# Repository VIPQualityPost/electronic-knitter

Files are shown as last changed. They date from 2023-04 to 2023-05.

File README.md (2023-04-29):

# Electronic Knitting Machine Controller
Inspired by the [Knitic project](https://github.com/mcanet/knitic), which 
seems to have mostly been abandoned. 
This board is to be a replacement for the mainboard within the machine, 
initially targeting Brother KH-930, KH-940 machines. While it disables the 
main touch controls, there is available a serial port which can control 
the patterns. Eventually, it would be nice to also design some 
compatibility with the original user interface panel. Additionally, the 
solenoid controls signals are exposed via HP 1650-63203 20-pin logic 
analyzer connector, either for debugging, or direct control of the 
solenoid array if you wish to just ignore the microcontroller on the 
board.

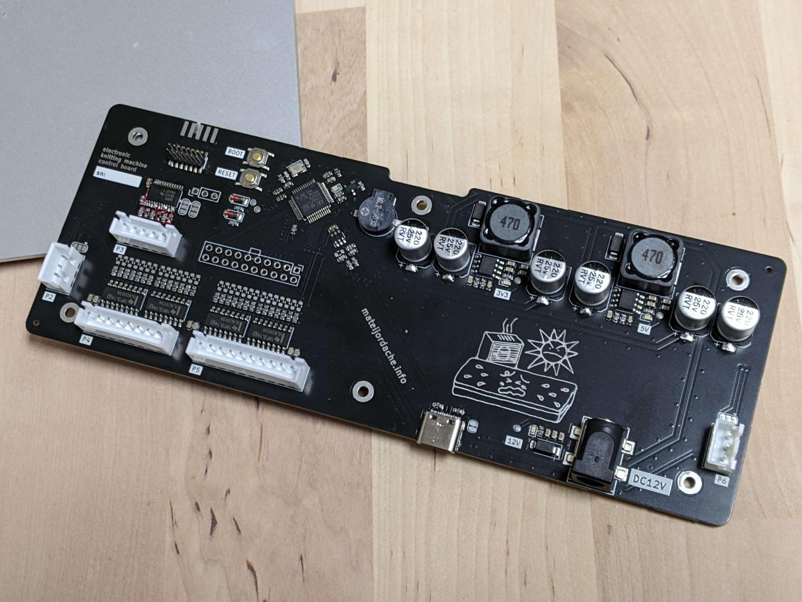
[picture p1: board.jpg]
Machine mainboard


This board also has a standalone power supply, so you can remove or ignore 
the transformer and power supply PCB built into the machine, which is 
quite heavy. 

Conveniently, the connectors used for the solenoid control as well as 
encoders and carriage signals fit modern JST-XH connectors, so these are 
compatible with the wiring assemblies already inside the machine.

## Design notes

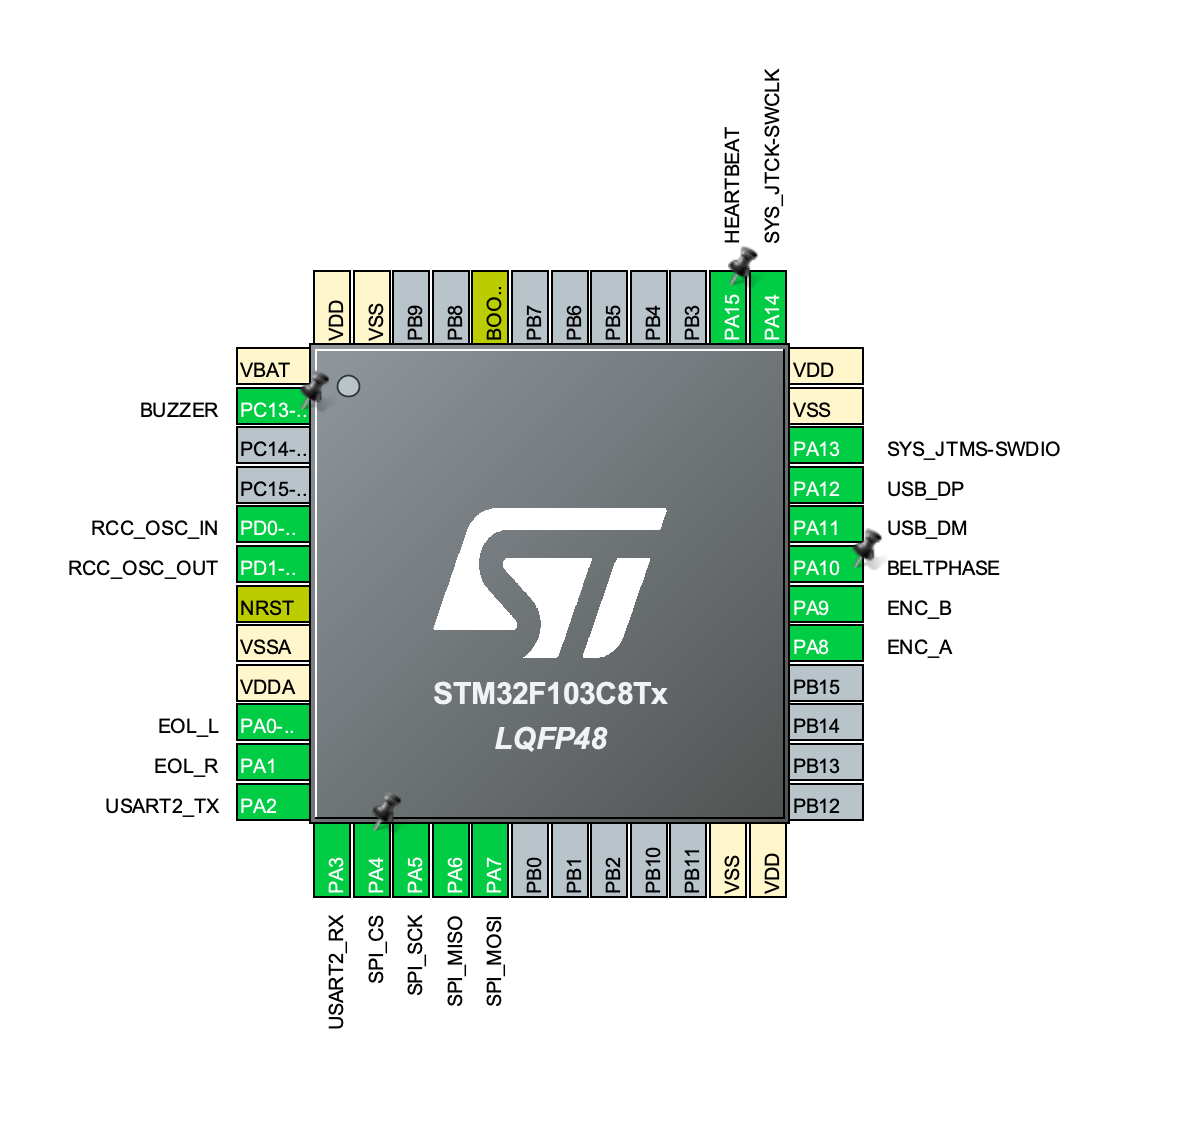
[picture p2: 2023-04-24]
hardware/Screenshot 2023-04-21 at 5.05.41 PM.png

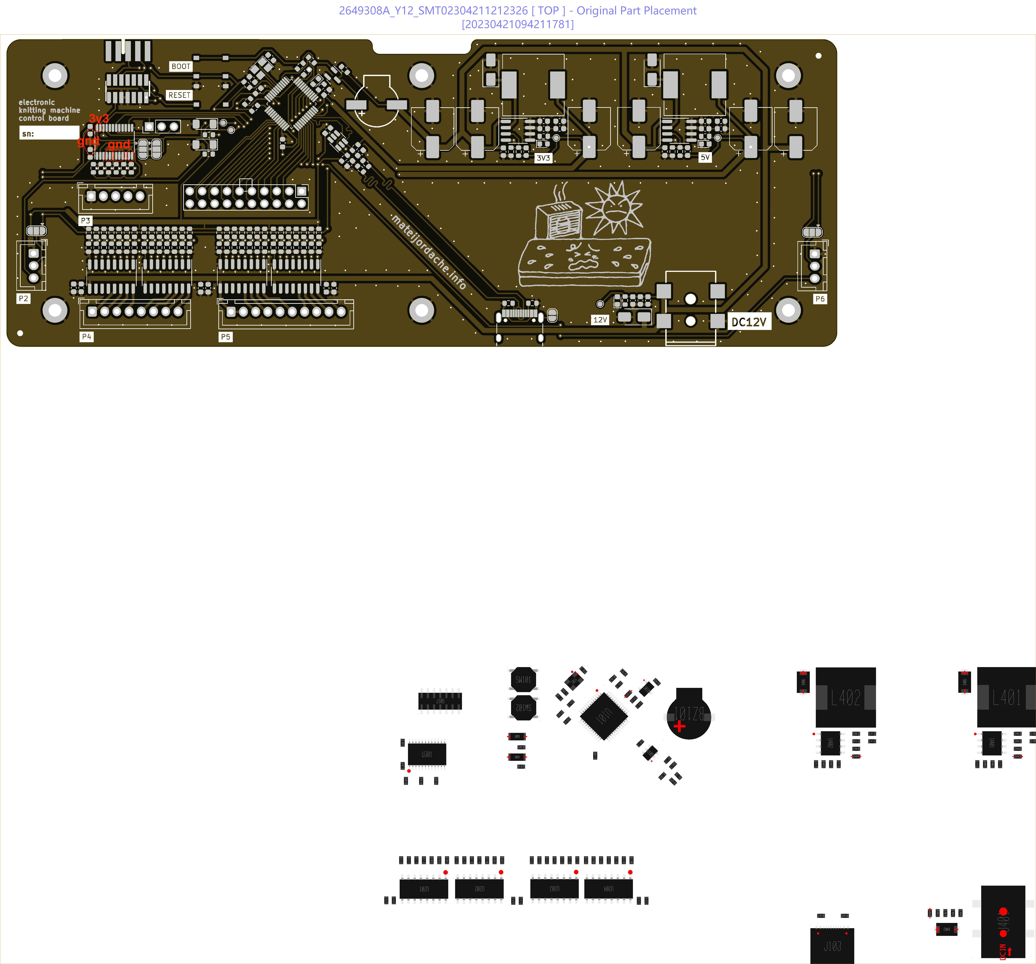
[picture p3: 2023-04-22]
hardware/rev1/ECO1.png

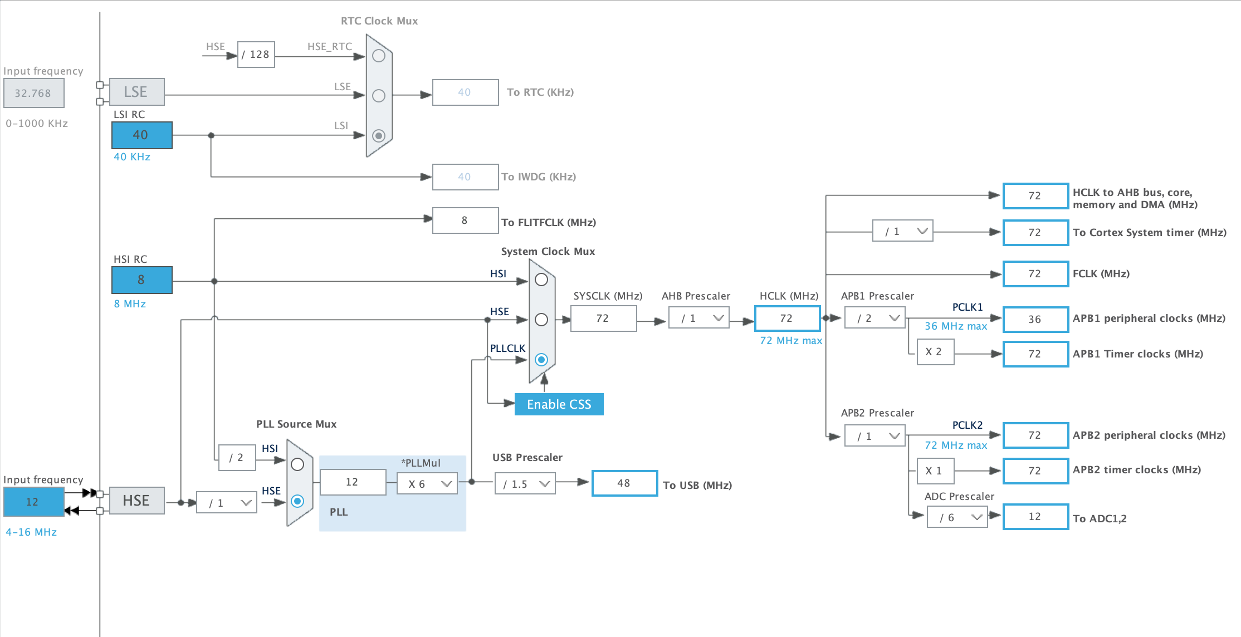
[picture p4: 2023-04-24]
hardware/Screenshot 2023-04-23 at 12.08.16 PM.png

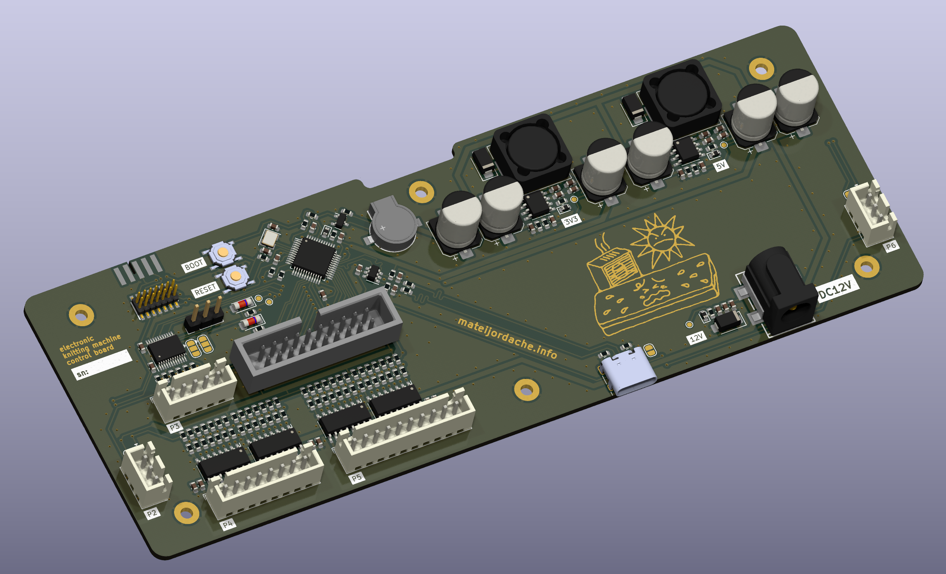
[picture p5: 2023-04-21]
render.png

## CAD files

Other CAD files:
hardware/kicad/electroknitter.FCStd

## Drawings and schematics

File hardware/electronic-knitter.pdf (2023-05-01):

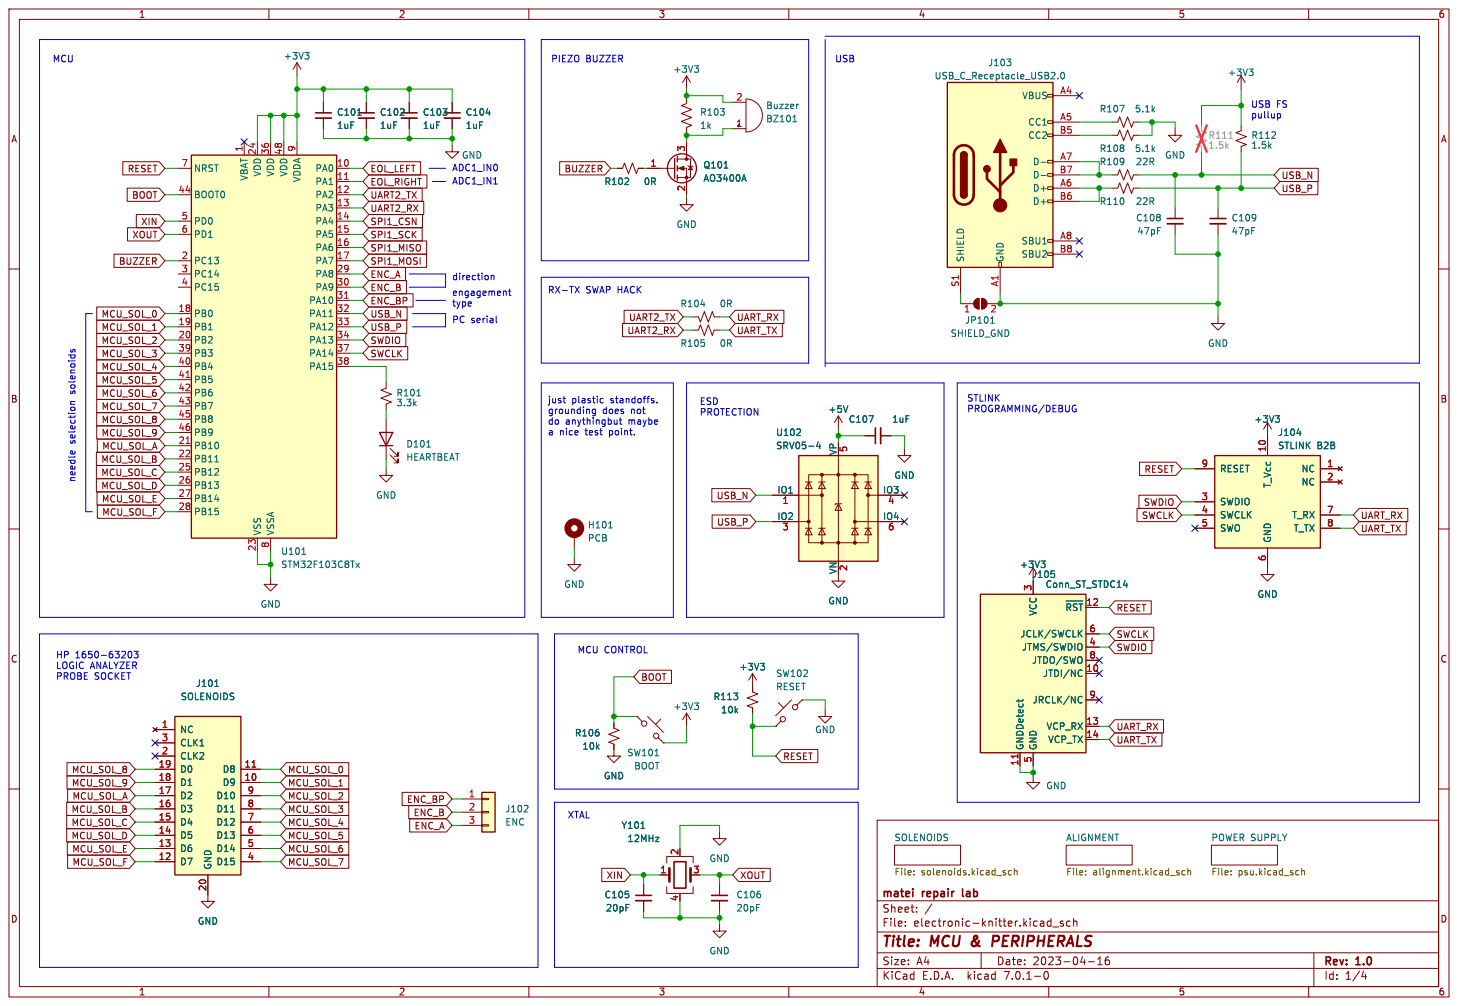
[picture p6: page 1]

1 PA0 10 PA1 11 PA2 12 PA3 13 PA4 14 PA5 15 PA6 16 PA7 17 PB0 18 PB1 19 PC13 2 PB2 20 PB10 21 PB11 22 VSS 23 VDD 24 PB12 25 PB13 26 PB14 27 PB15 28 PA8 29 PC14 3 PA9 30 PA10 31 PA11 32 PA12 33 PA13 34 VDD 36 PA14 37 PA15 38 PB3 39 PC15 4 PB4 40 PB5 41 PB6 42 PB7 43 BOOT0 44 PB8 45 PB9 46 VDD 48 PD0 5 PD1 6 NRST 7 VSSA

RX-TX SWAP HACK

File: solenoids.kicad_sch
File: electronic-knitter.kicad_sch Sheet: / matei repair lab

Id: 1/4 Title: MCU & PERIPHERALS

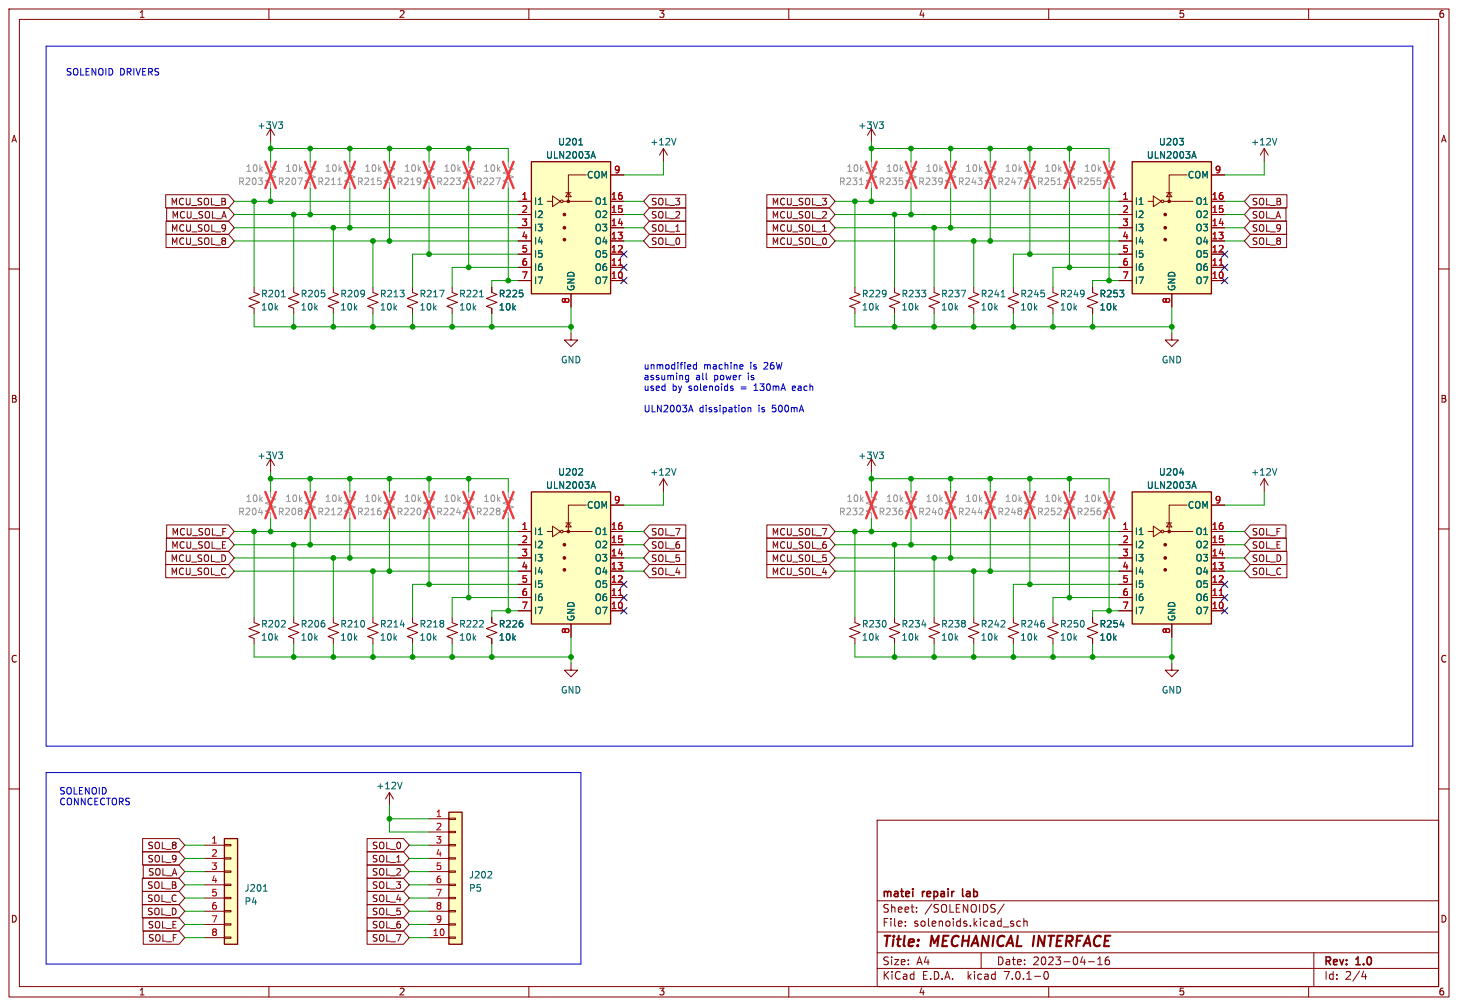
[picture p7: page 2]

File: solenoids.kicad_sch Sheet: /SOLENOIDS/ matei repair lab

Id: 2/4 Title: MECHANICAL INTERFACE

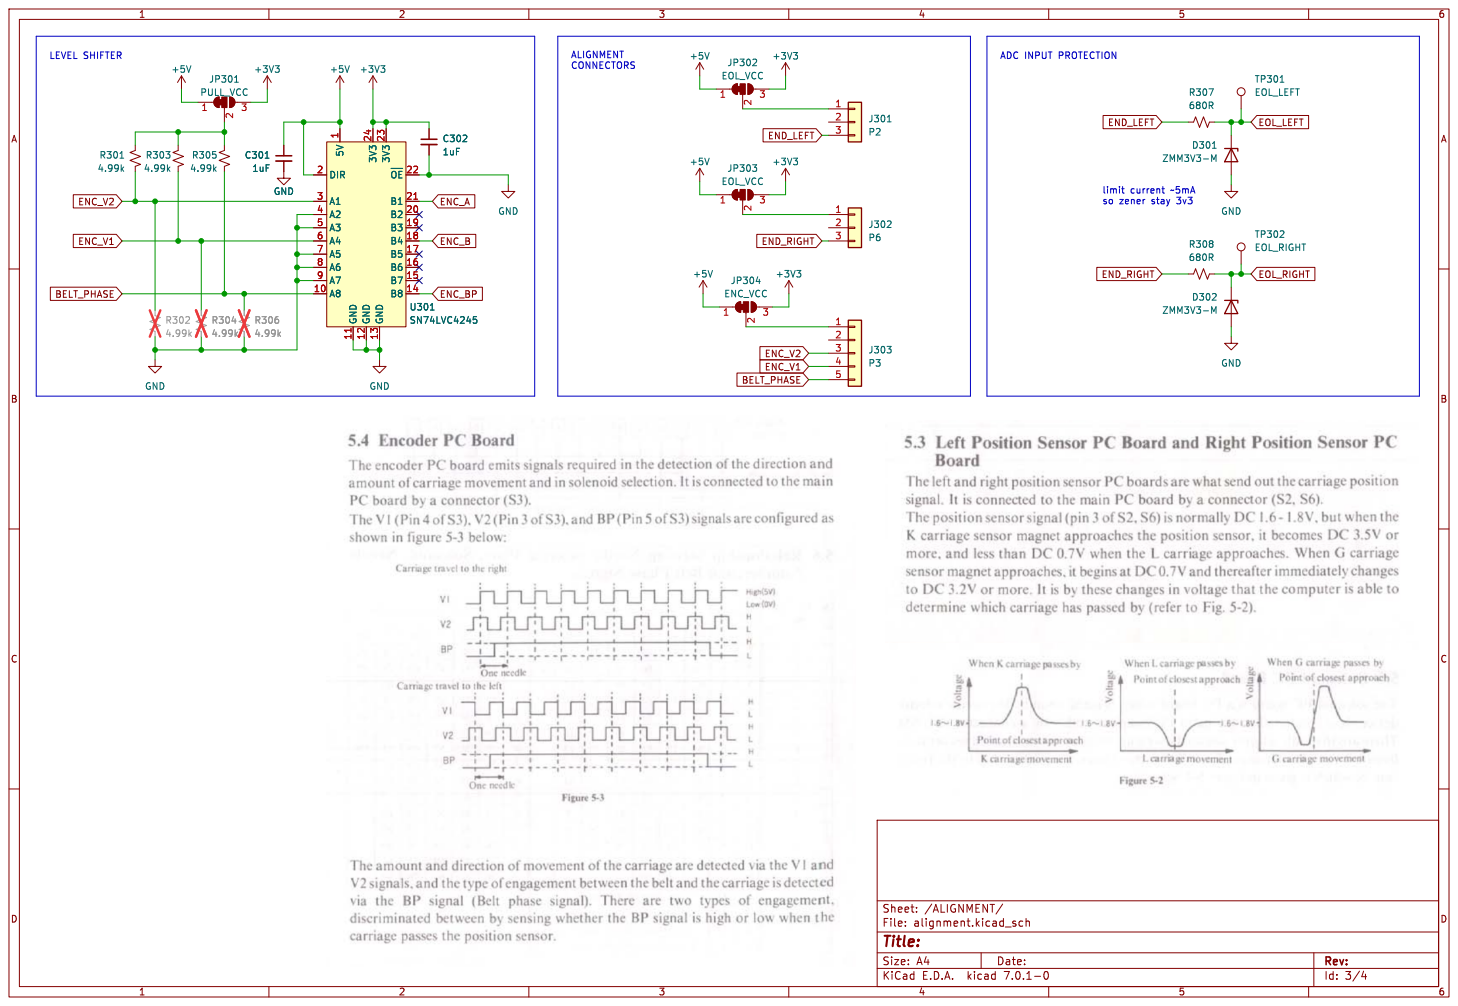
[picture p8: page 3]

Id: 3/4 Title: File: alignment.kicad_sch Sheet: /ALIGNMENT/

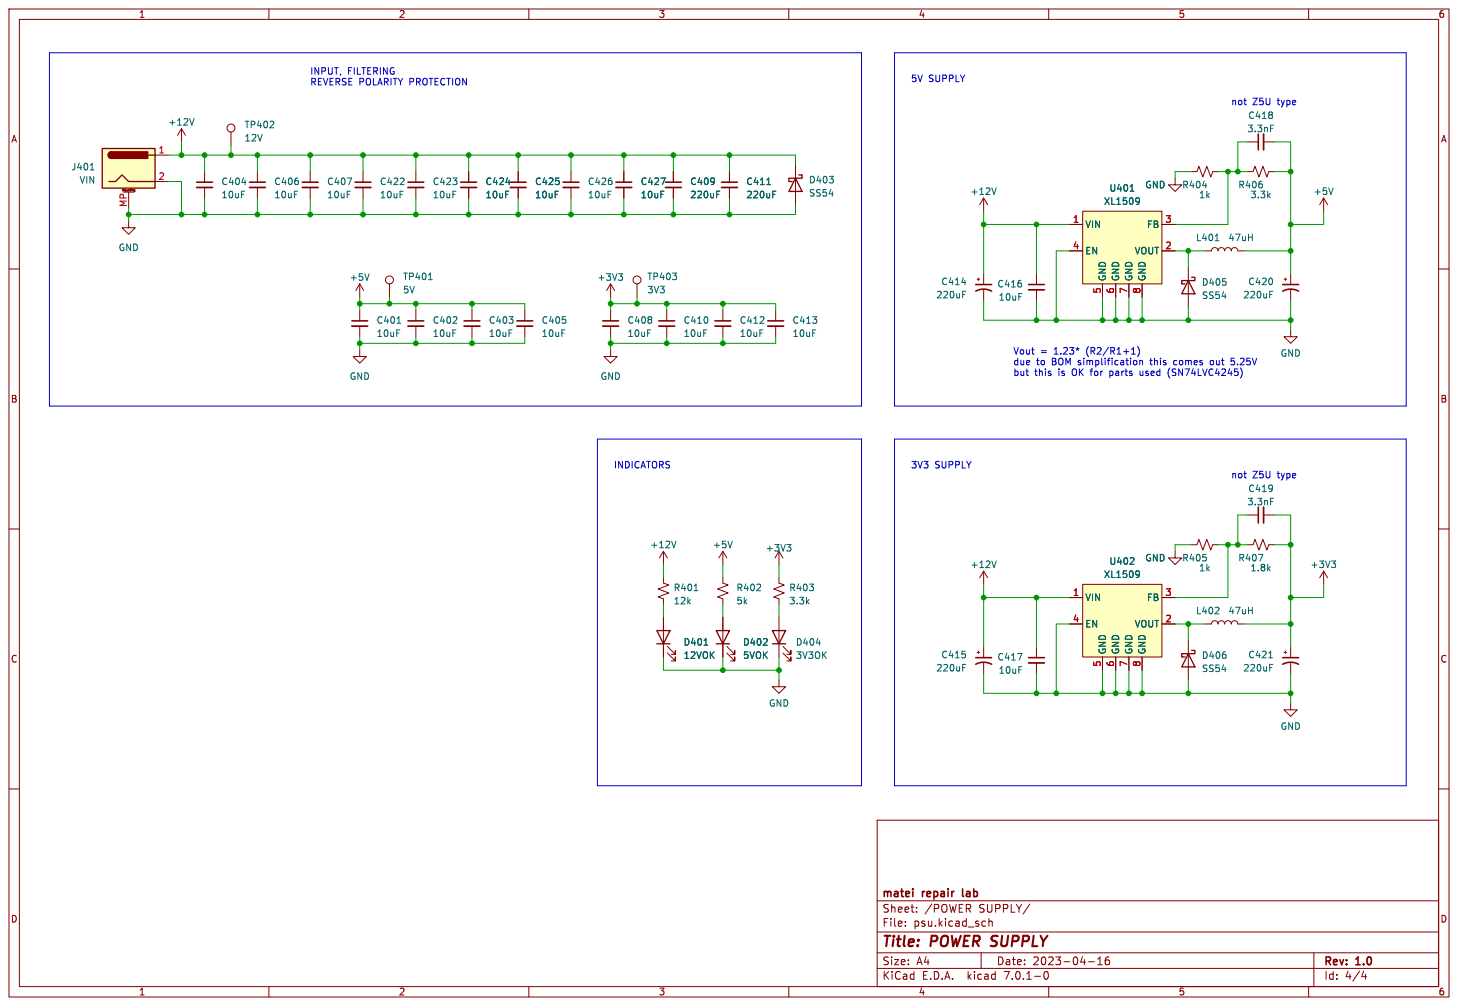
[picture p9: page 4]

but this is OK for parts used (SN74LVC4245) 5V SUPPLY

8 VIN 1 VOUT 2 FB 3 EN 4 U401 XL1509 +12V

8 VIN 1 VOUT 2 FB 3 EN 4

8 VIN 1 VOUT 2 FB 3 EN 4 U402 XL1509 R407

8 VIN 1 VOUT 2 FB 3 EN 4 GND

Id: 4/4 Title: POWER SUPPLY

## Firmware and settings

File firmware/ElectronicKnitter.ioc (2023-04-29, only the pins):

Mcu.UserName=STM32F103C8Tx
PA0-WKUP.GPIO_Label=EOL_L
PA0-WKUP.Signal=ADCx_IN0
PA1.GPIO_Label=EOL_R
PA1.Signal=ADCx_IN1
PA10.GPIO_Label=BELTPHASE
PA10.Signal=GPXTI10
PA11.Signal=USB_DM
PA12.Signal=USB_DP
PA13.Signal=SYS_JTMS-SWDIO
PA14.Signal=SYS_JTCK-SWCLK
PA15.GPIO_Label=HEARTBEAT
PA15.Signal=S_TIM2_CH1_ETR
PA2.Signal=USART2_TX
PA3.Signal=USART2_RX
PA4.GPIO_Label=SPI_CS
PA4.Signal=GPIO_Output
PA5.GPIO_Label=SPI_SCK
PA5.Signal=SPI1_SCK
PA6.GPIO_Label=SPI_MISO
PA6.Signal=SPI1_MISO
PA7.GPIO_Label=SPI_MOSI
PA7.Signal=SPI1_MOSI
PA8.GPIO_Label=ENC_A
PA8.Signal=S_TIM1_CH1
PA9.GPIO_Label=ENC_B
PA9.Signal=S_TIM1_CH2
PC13-TAMPER-RTC.GPIO_Label=BUZZER
PC13-TAMPER-RTC.Signal=GPIO_Output
PD0-OSC_IN.Signal=RCC_OSC_IN
PD1-OSC_OUT.Signal=RCC_OSC_OUT

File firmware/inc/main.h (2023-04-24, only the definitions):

#define BUZZER_Pin GPIO_PIN_13
#define BUZZER_GPIO_Port GPIOC
#define EOL_L_Pin GPIO_PIN_0
#define EOL_L_GPIO_Port GPIOA
#define EOL_R_Pin GPIO_PIN_1
#define EOL_R_GPIO_Port GPIOA
#define SPI_CS_Pin GPIO_PIN_4
#define SPI_CS_GPIO_Port GPIOA
#define SPI_SCK_Pin GPIO_PIN_5
#define SPI_SCK_GPIO_Port GPIOA
#define SPI_MISO_Pin GPIO_PIN_6
#define SPI_MISO_GPIO_Port GPIOA
#define SPI_MOSI_Pin GPIO_PIN_7
#define SPI_MOSI_GPIO_Port GPIOA
#define ENC_A_Pin GPIO_PIN_8
#define ENC_A_GPIO_Port GPIOA
#define ENC_B_Pin GPIO_PIN_9
#define ENC_B_GPIO_Port GPIOA
#define BELTPHASE_Pin GPIO_PIN_10
#define BELTPHASE_GPIO_Port GPIOA
#define HEARTBEAT_Pin GPIO_PIN_15
#define HEARTBEAT_GPIO_Port GPIOA

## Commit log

2023-04-17 create repo
    [alignment.kicad_sch, electronic-knitter.kicad_sch, needleselectors.kicad_sch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]
2023-04-20 finish layout
    [alignment.kicad_sch, psu.kicad_sch, solenoids.kicad_sch]
2023-04-21 finalize fab files and order first rev of board
    [alignment.kicad_sch, electronic-knitter.kicad_sch, solenoids.kicad_sch]
2023-04-21 update schematic
2023-04-21 fix SN74LVC4245 footprint
2023-04-21 add interactive BOM
2023-04-22 start on firmware
    [alignment.kicad_sch, electronic-knitter.kicad_sch, psu.kicad_sch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]
2023-04-24 fix project with stm32pio
    [electronic-knitter.kicad_sch]
2023-04-29 bring up board, supplies, USB, ADC, DMA working
2023-04-30 Auto-commit Sun Apr 30 10:54:47 EDT 2023
    [electroknitter.FCStd]
2023-05-01 work on firmware and swap solenoid banks to match actual pinout
    [alignment.kicad_sch, electronic-knitter.kicad_sch, psu.kicad_sch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]
2023-05-04 fix belt phase logic

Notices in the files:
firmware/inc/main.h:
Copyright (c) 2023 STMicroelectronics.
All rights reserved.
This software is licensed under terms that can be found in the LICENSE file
